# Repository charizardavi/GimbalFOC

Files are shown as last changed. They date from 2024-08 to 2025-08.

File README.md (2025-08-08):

# GimbalFOC

pcb image

## Sponsored By
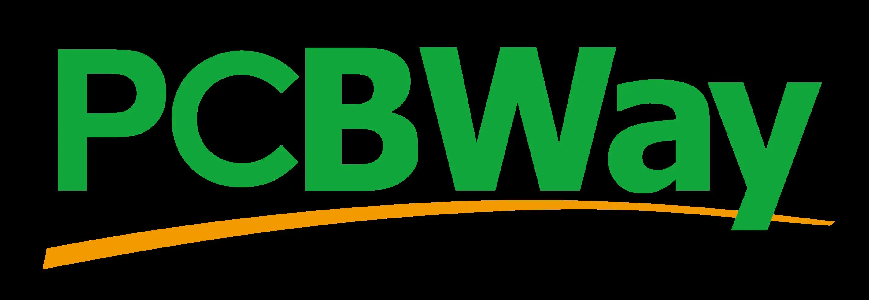
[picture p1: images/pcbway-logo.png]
pcbway logo


A gimbal BLDC controller:
- MCU: ESP32-S3 (XIAO)
- Motor Controller: DRV8813

## Other Parts
- [BLDC](https://shop.iflight.com/gimbal-motors-cat44/ipower-motor-gm4108h-120t-brushless-gimbal-motor-pro217)
- Battery: Tested with 4S LiPO

## Completed
- V1
- V2 (much smaller PCB, addition of ESP32S3)

## TODO
- Build and test 3-axis

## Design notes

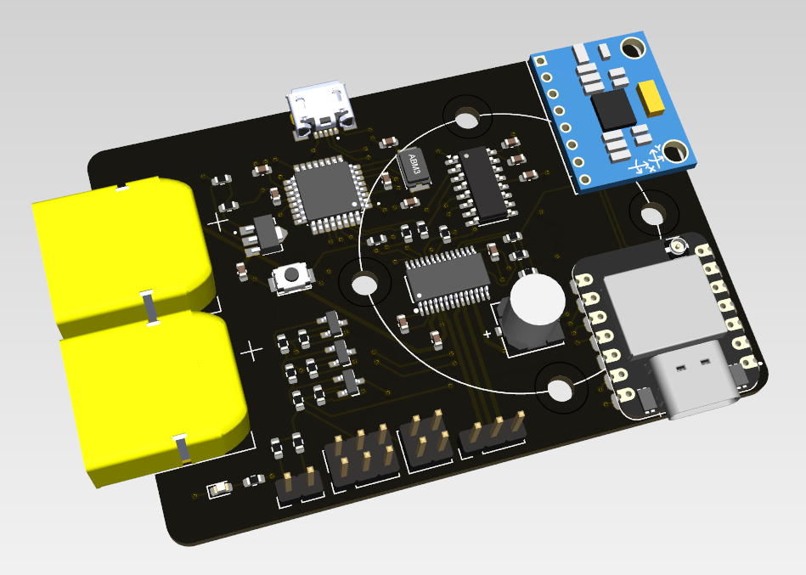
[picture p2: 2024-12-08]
images/kicad_preview.png

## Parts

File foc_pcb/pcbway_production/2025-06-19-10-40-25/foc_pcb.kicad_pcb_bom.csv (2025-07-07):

Designator | Quantity | Value | Footprint | Package | MPN | DNP | Mount_Type | Description | MF | Purchase-URL | Check_prices | STANDARD | PARTREV | SnapEDA_Link | MP | Description_1 | MANUFACTURER | DigiKey_Part_Number | SNAPEDA_PACKAGE_ID | MAXIMUM_PACKAGE_HEIGHT | Manufacturer Part | Manufacturer | Supplier Part | Supplier | LCSC Part Name
C1, C2, C4 | 3 | 100nF | C_0603_1608Metric |  |  |  | smt | Unpolarized capacitor
C3 | 1 | .1uF | C_0603_1608Metric |  |  |  | smt | Unpolarized capacitor
C5 | 1 | UWT1V101MCL1GS | PCAP_6.3x7.7-ELECT_NCA-L |  |  |  | smt | Polarized capacitor, US symbol
C6 | 1 | 470nF | C_0603_1608Metric |  |  |  | smt | Unpolarized capacitor
D1 | 1 | LED | LED_0603_1608Metric |  |  |  | smt | Light emitting diode
D2 | 1 | 1N5819HW-7-F | SOD3715X145N | None |  |  | smt |  | Diodes Zetex | https://www.snapeda.com/api/url_track_click_mouser/?unipart_id=4796063&manufacturer=Diodes Zetex&part_name=1N5819HW-7-F&search_term=None | https://www.snapeda.com/parts/1N5819HW-7-F/Zetex/view-part/?ref=eda | IPC-7351B | 18-2 | https://www.snapeda.com/parts/1N5819HW-7-F/Zetex/view-part/?ref=snap | 1N5819HW-7-F | Diode Schottky 40V 1A 2-Pin SOD-123 T/R | Diodes Inc.
J1 | 1 | Conn_01x03 | PinHeader_1x03_P2.54mm_Vertical |  |  |  | tht | Generic connector, single row, 01x03, script generated (kicad-library-utils/schlib/autogen/connector/)
J2 | 1 | BATT_IN | JST_VH_B2P-VH_1x02_P3.96mm_Vertical |  |  |  | tht | Generic connector, single row, 01x02, script generated (kicad-library-utils/schlib/autogen/connector/)
J3 | 1 | power_supply | PinHeader_2x02_P2.54mm_Vertical |  |  |  | tht | Generic connector, double row, 02x02, counter clockwise pin numbering scheme (similar to DIP package numbering), script generated (kicad-library-utils/schlib/autogen/connector/)
J4 | 1 | IMU | PinHeader_1x04_P2.00mm_Vertical |  |  |  | tht | Generic connector, single row, 01x04, script generated (kicad-library-utils/schlib/autogen/connector/)
J5 | 1 | ESP | PinHeader_1x04_P2.00mm_Vertical |  |  |  | tht | Generic connector, single row, 01x04, script generated (kicad-library-utils/schlib/autogen/connector/)
R1, R6, R8, R9 | 4 | 10k | R_0603_1608Metric |  |  |  | smt | Resistor
R10, R11 | 2 | 4.7k | R_0603_1608Metric |  |  |  | smt | Resistor
R2, R5, R7 | 3 | 1k | R_0603_1608Metric |  |  |  | smt | Resistor
R3 | 1 | 200 | R_0603_1608Metric |  |  |  | smt | Resistor
R4 | 1 | 590 | R_0603_1608Metric |  |  |  | smt | Resistor
U1 | 1 | DRV8313PWPR | HTSSOP-28_L9.8-W4.5-P0.65-LS6.6-BL-EP | HTSSOP-28 Texas Instruments |  |  | tht | 65-V max 3-A peak 3-phase motor driver with integrated FETs | Texas Instruments |  | https://www.snapeda.com/parts/DRV8313PWPR/Texas+Instruments/view-part/?ref=eda | Manufacturer Recommendations | D | https://www.snapeda.com/parts/DRV8313PWPR/Texas+Instruments/view-part/?ref=snap | DRV8313PWPR |  | Texas Instruments | 296-40072-2-ND | 102627 | 1.2 mm
U2 | 1 | ~ | SOP-8_L4.9-W3.9-P1.27-LS6.0-BL |  |  |  | tht |  |  |  |  |  |  |  |  |  |  |  |  |  | MT6701CT-STD | MagnTek(麦歌恩) | C2856764 | LCSC | 霍尔在线编程角度位置传感器
U3 | 1 | ~ | MOUDLE14P-SMD-2.54-21X17.8MM |  |  |  | tht
VR1 | 1 | LM317LCPK | VREG_LM317LCPK | SOT-89-3 Texas Instruments |  |  | smt |  | Texas Instruments | https://www.snapeda.com/api/url_track_click_mouser/?unipart_id=354472&manufacturer=Texas Instruments&part_name=LM317LCPK&search_term=None | https://www.snapeda.com/parts/LM317LCPK/Texas+Instruments/view-part/?ref=eda | Manufacturer Recommendations | E | https://www.snapeda.com/parts/LM317LCPK/Texas+Instruments/view-part/?ref=snap | LM317LCPK | 100-mA, 35-V, adjustable linear voltage regulator | Texas Instruments | 296-26093-2-ND | 102648 | 1.6 mm

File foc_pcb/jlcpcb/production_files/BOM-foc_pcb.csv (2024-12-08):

Comment | Designator | Footprint | LCSC
10k | R19 | R_0603_1608Metric
.1uF | C4 | C_0603_1608Metric
UWT1V101MCL1GS | C11 | PCAP_6.3x7.7-ELECT_NCA-L
1k | R7 | R_0603_1608Metric
BSS138-7-F | U3 | SOT95P240X110-3N
10k | R17 | R_0603_1608Metric
power_supply | J4 | PinHeader_2x02_P2.54mm_Vertical
1k | R6 | R_0603_1608Metric
SW_Push | SW1 | SW-SMD_L4.0-W3.0-LS4.6
200 | R13 | R_0603_1608Metric
10k | R2 | R_0603_1608Metric
BSS138-7-F | U4 | SOT95P240X110-3N
100nF | C9 | C_0603_1608Metric
10118193-0001LF | J12 | AMPHENOL_10118193-0001LF
XT60PW-M | J5 | AMASS_XT60PW-M
MPU6050 | J1 | PinHeader_1x08_P2.54mm_Vertical
100nF | C2 | C_0603_1608Metric
Conn_01x03 | J3 | PinHeader_1x03_P2.54mm_Vertical
DRV8313PWPR | U1 | HTSSOP-28_L9.8-W4.5-P0.65-LS6.6-BL-EP
10k | R15 | R_0603_1608Metric
1nF | C10 | C_0603_1608Metric
10k | R12 | R_0603_1608Metric
10k | R5 | R_0603_1608Metric
LED | D5 | LED_0603_1608Metric
100nF | C7 | C_0603_1608Metric
~ | U6 | MOUDLE14P-SMD-2.54-21X17.8MM
10k | R18 | R_0603_1608Metric
10nF | C12 | C_0603_1608Metric
22pF | C16 | C_0603_1608Metric
1k | R10 | R_0603_1608Metric
ABM3-16MHZ | Y1 | XTAL_ABM3-16.000MHZ-B2-T
100nF | C8 | C_0603_1608Metric
ATMEGA328P-AU | U2 | QFP80P900X900X120-32N
LM317LCPK | VR1 | VREG_LM317LCPK
10k | R1 | R_0603_1608Metric
Conn_01x02 | J2 | PinHeader_1x02_P2.54mm_Vertical
10k | R3 | R_0603_1608Metric
BSS138-7-F | U7 | SOT95P240X110-3N
22pF | C17 | C_0603_1608Metric
10k | R16 | R_0603_1608Metric
XT60PW-M | J6 | AMASS_XT60PW-M
CH340C | U5 | SOIC-16_3.9x9.9mm_P1.27mm
100nF | C3 | C_0603_1608Metric
10k | R20 | R_0603_1608Metric
10k | R8 | R_0603_1608Metric
10k | R4 | R_0603_1608Metric
100nF | C6 | C_0603_1608Metric
Conn_02x03_Top_Bottom | J10 | PinHeader_2x03_P2.54mm_Vertical
470nF | C1 | C_0603_1608Metric
590 | R14 | R_0603_1608Metric
1uF | C14 | C_0603_1608Metric
100nF | C13 | C_0603_1608Metric
AS5600-ASOT | IC1 | SOIC127P600X175-8N
4.7k | R9 | R_0603_1608Metric
4.7k | R11 | R_0603_1608Metric

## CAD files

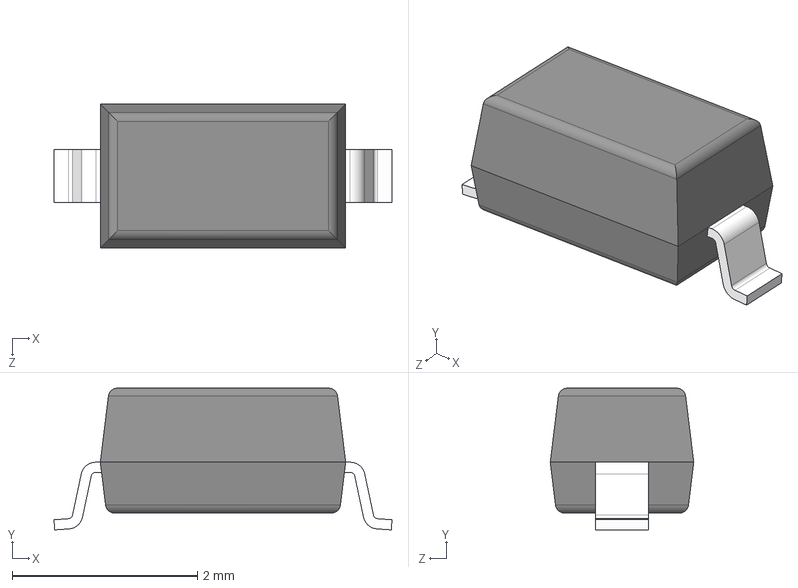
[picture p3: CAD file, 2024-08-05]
foc_pcb/parts_lib/1N5819HW-7-F/1N5819HW-7-F.step
3.65 x 1.53 x 1.55 mm

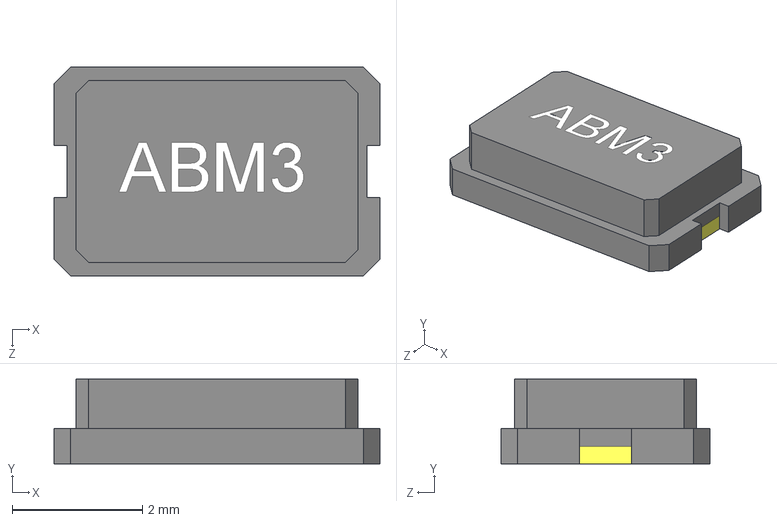
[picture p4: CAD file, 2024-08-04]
foc_pcb/parts_lib/ABM3-16.000MHZ-B2-T/ABM3-16.000MHZ-B2-T.step
5.00 x 1.30 x 3.20 mm

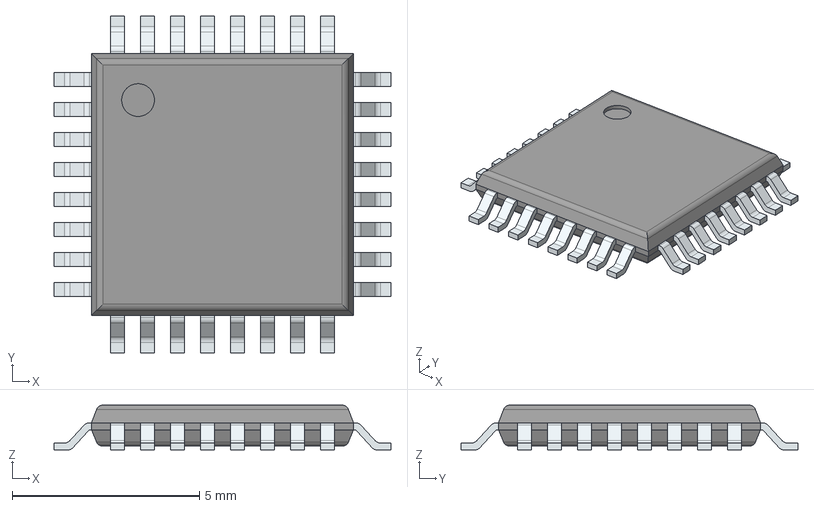
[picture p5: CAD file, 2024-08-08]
foc_pcb/parts_lib/ATMEGA328P-AU-NEW/ATMEGA328P-AU.stp
9.00 x 9.00 x 1.20 mm
PinsArrayLR
PinsArrayTB

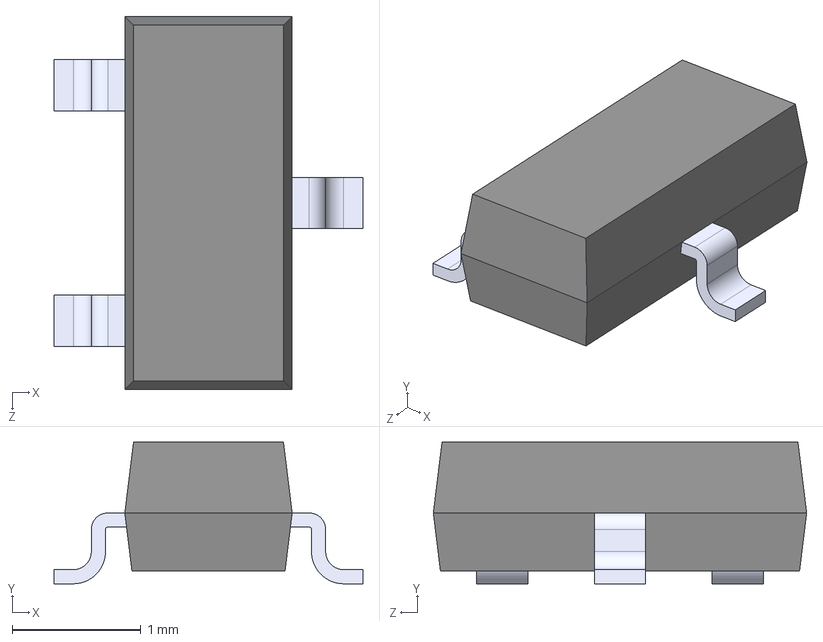
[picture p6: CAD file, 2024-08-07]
foc_pcb/parts_lib/BSS138-7-F/BSS138-7-F.step
2.40 x 1.10 x 2.90 mm

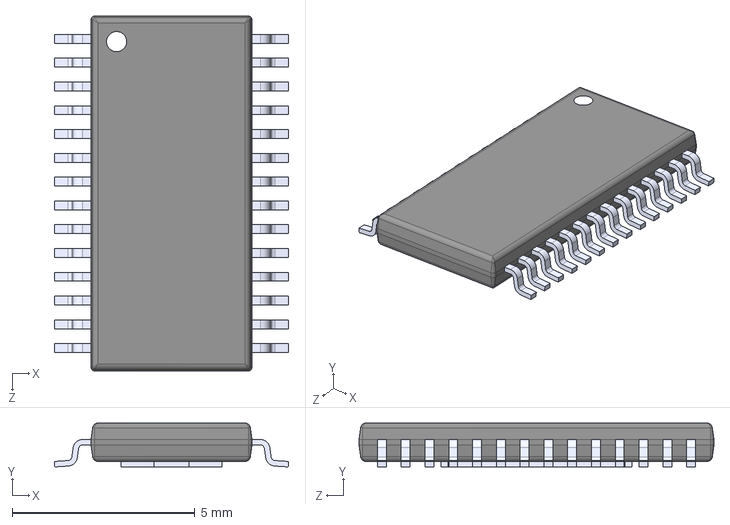
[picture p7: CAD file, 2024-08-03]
foc_pcb/parts_lib/DRV8313PWPR/DRV8313PWPR.step
6.40 x 1.20 x 9.70 mm

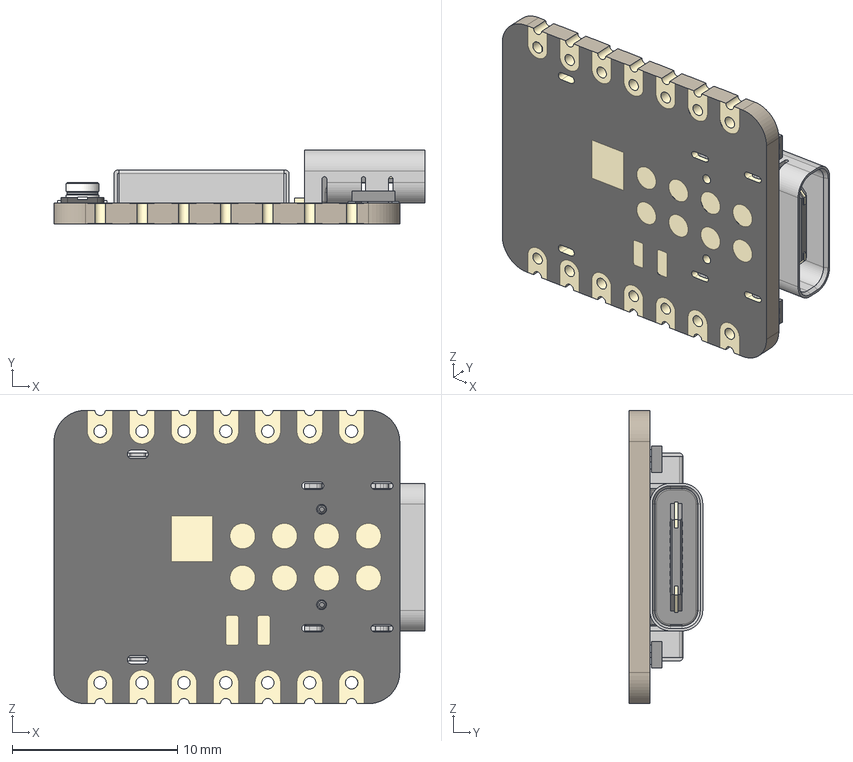
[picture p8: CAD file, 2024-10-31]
foc_pcb/parts_lib/ESP32S3/XIAO-ESP32S3 v2.step
22.5 x 4.46 x 17.8 mm
BOSS-EXTRUDE14_8_
BOSS-EXTRUDE7_4_
BOSS-EXTRUDE7_3_
BOSS-EXTRUDE14_4_
BOSS-EXTRUDE14_2_
BOSS-EXTRUDE14_11_
BOSS-EXTRUDE7_7_
BOSS-EXTRUDE14_9_
BOSS-EXTRUDE14_3_
BOSS-EXTRUDE14_7_
MIRROR2
BOSS-EXTRUDE14_5_
BOSS-EXTRUDE14_12_
BOSS-EXTRUDE7_8_
BOSS-EXTRUDE7_1_
BOSS-EXTRUDE14_10_
BOSS-EXTRUDE7_9_
BOSS-EXTRUDE14_6_
BOSS-EXTRUDE14_1_
BOSS-EXTRUDE7_6_
BOSS-EXTRUDE7_2_
CUT-EXTRUDE5
BOSS-EXTRUDE7_5_
Shield
Pins x 2
U.FL-R-SMT-1_10_ v1

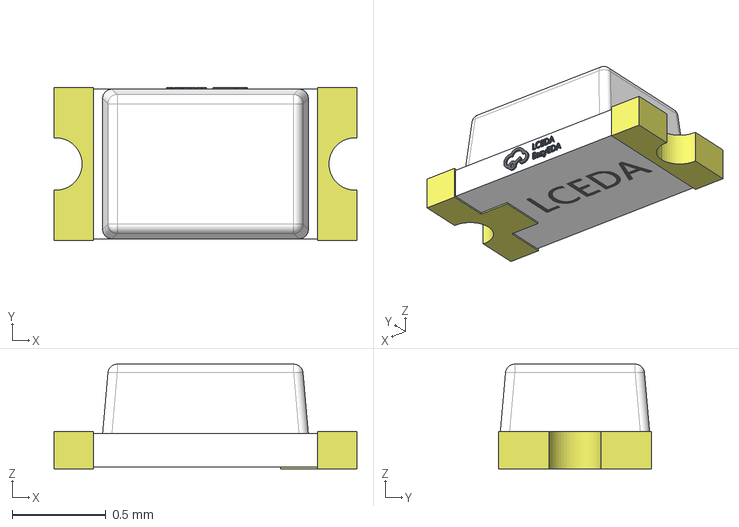
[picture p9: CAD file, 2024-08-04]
foc_pcb/parts_lib/KT-0603R/KT-0603R.step
1.62 x 0.82 x 0.56 mm

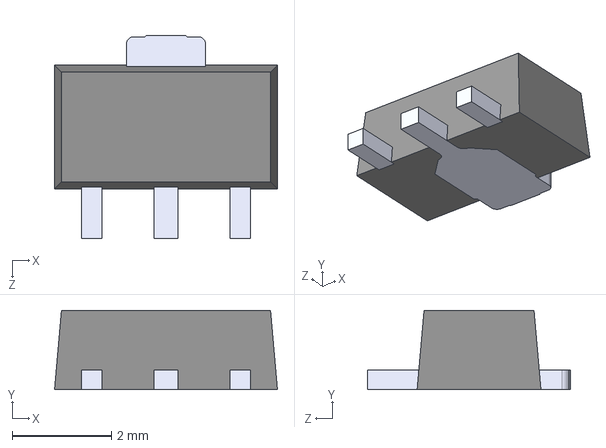
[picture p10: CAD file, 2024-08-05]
foc_pcb/parts_lib/LM317LCPK/LM317LCPK.step
4.50 x 1.60 x 4.09 mm

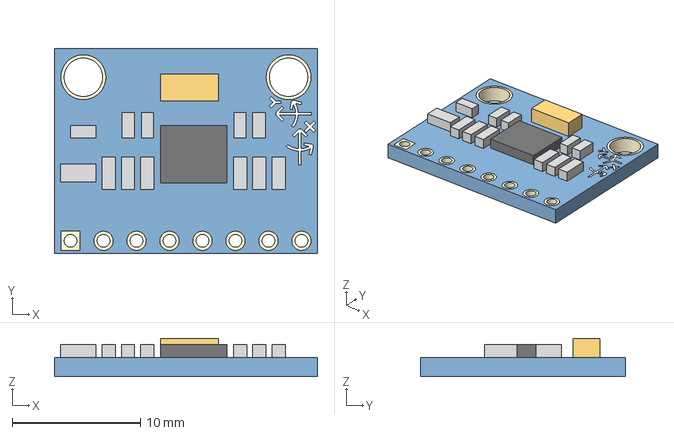
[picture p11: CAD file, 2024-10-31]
foc_pcb/parts_lib/MPU_6050/MPU_6050.step
20.5 x 16.0 x 3.00 mm

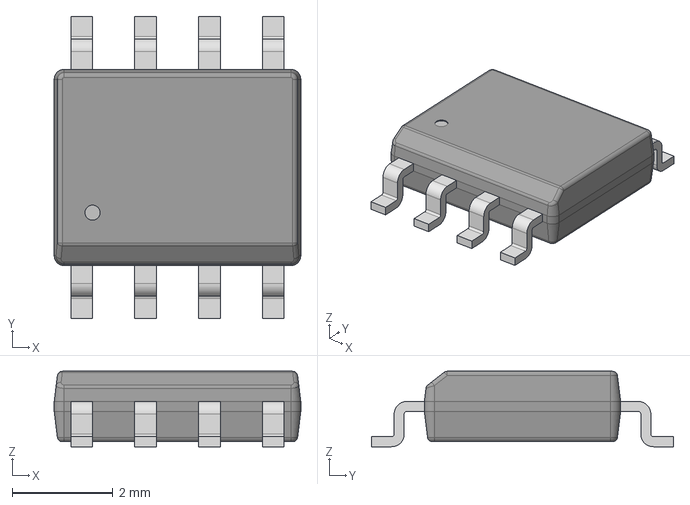
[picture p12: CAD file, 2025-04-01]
foc_pcb/parts_lib/MT6701CT-STD/MT6701CT-STD.step
4.90 x 6.00 x 1.50 mm

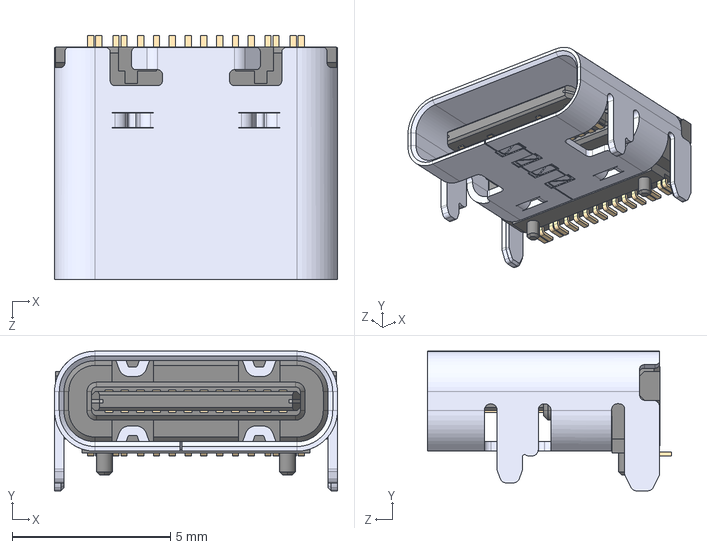
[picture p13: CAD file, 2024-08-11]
foc_pcb/parts_lib/USB4105-GF-A/USB4105-GF-A.step
8.94 x 4.41 x 7.71 mm

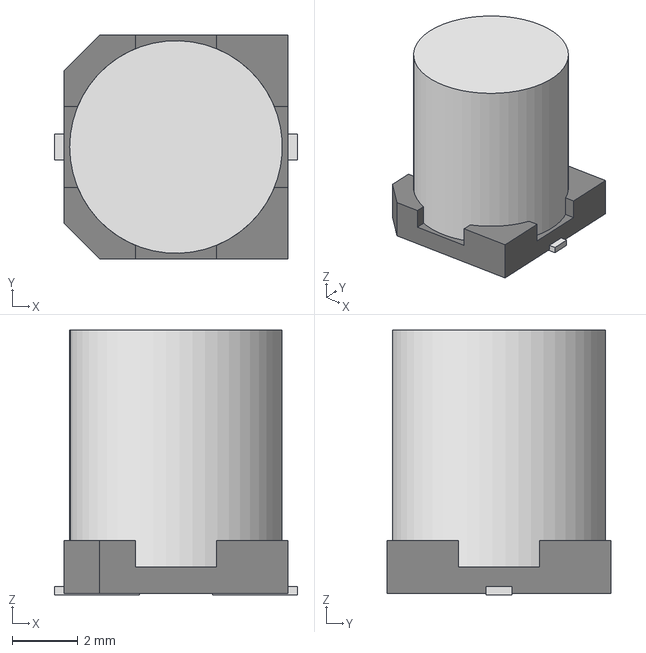
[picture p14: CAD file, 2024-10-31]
foc_pcb/parts_lib/UWT1V101MCL1GS/PCAP_6_3x7_7-ELECT_NCA.step
7.39 x 6.81 x 8.05 mm

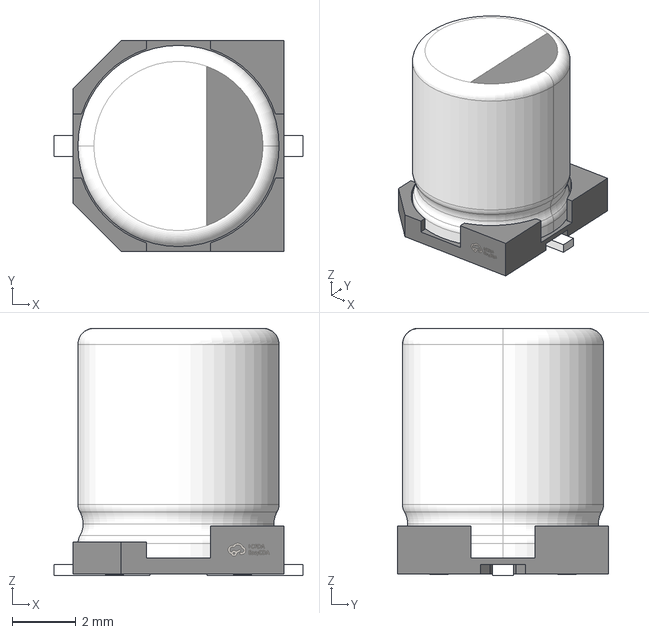
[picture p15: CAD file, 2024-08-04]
foc_pcb/parts_lib/VT1V101M-CRE77/VT1V101M-CRE77.step
7.80 x 6.60 x 7.75 mm

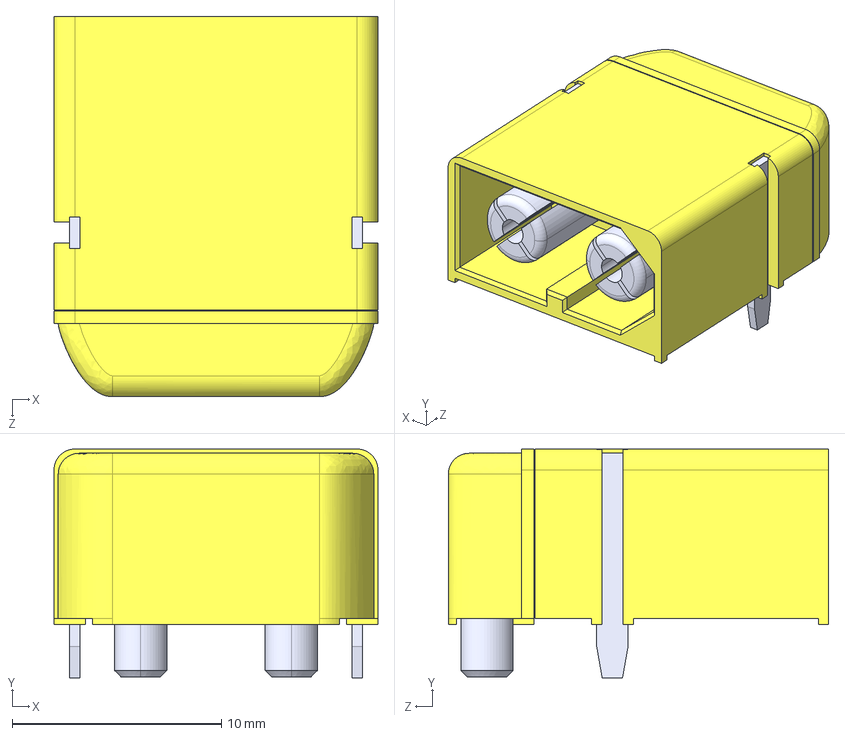
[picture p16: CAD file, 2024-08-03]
foc_pcb/parts_lib/XT60PW-M/XT60PW-M.step
15.5 x 11.0 x 18.2 mm

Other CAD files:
foc_pcb/parts_lib/ATMEGA328P-AU/ATMEGA328P-AU.step
foc_pcb/parts_lib/simpleFOC_led/simplefoc_LED.step
foc_pcb/parts_lib/YTS-A011-2B/YTS-A011-2B.step
foc_pcb/parts_lib/usbMicroB/10118193-0001LF.step

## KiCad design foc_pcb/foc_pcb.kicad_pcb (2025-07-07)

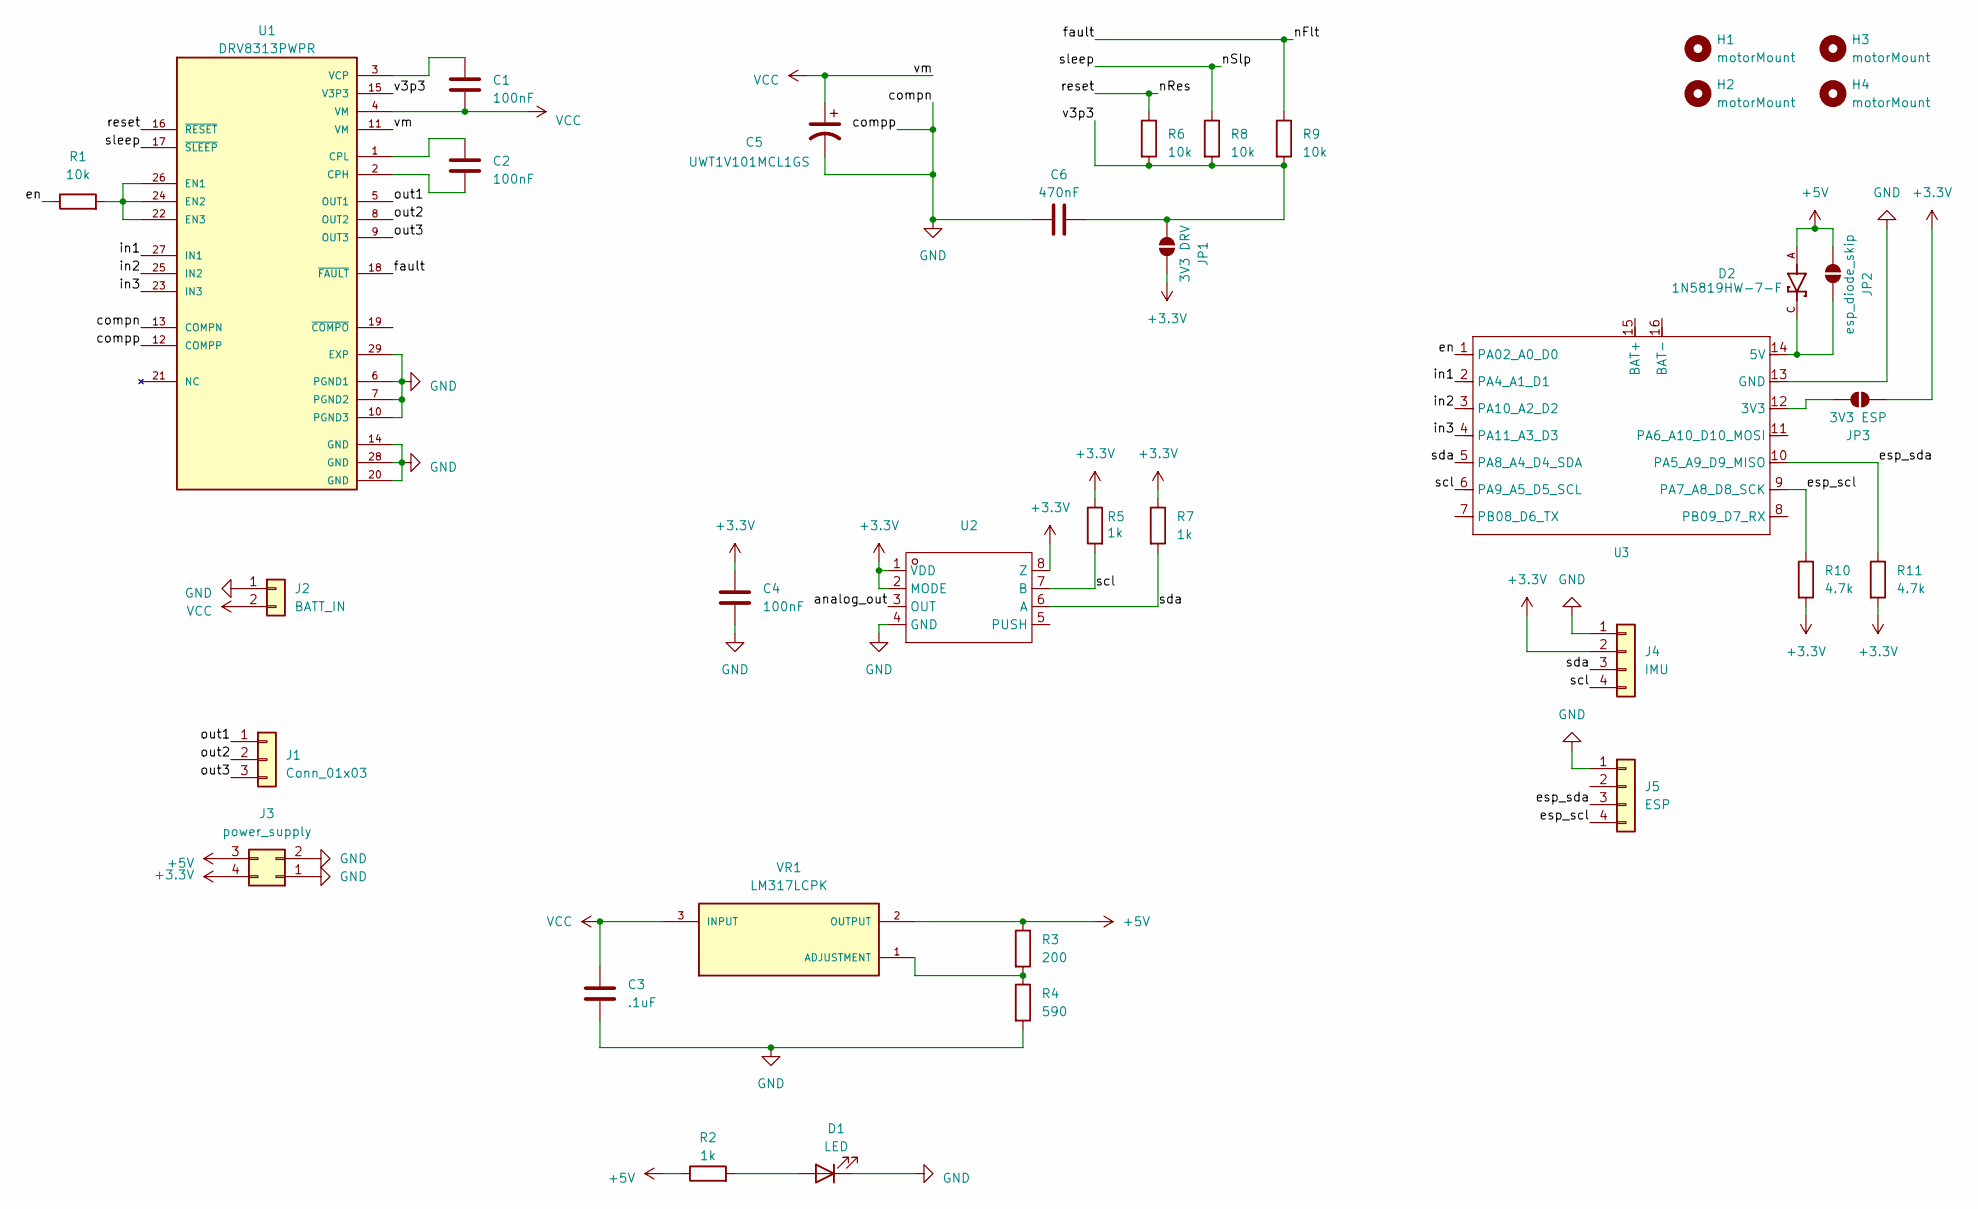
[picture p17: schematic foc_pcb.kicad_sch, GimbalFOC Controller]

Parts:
C1, C2, C4: 100nF; C_0603_1608Metric
C3: .1uF; C_0603_1608Metric
C5: UWT1V101MCL1GS; PCAP_6.3x7.7-ELECT_NCA-L
C6: 470nF; C_0603_1608Metric
D1: LED; LED_0603_1608Metric
D2: 1N5819HW-7-F; SOD3715X145N; PARTREV 18-2
H1, H2, H3, H4: motorMount; MountingHole_3.2mm_M3
J1: Conn_01x03; PinHeader_1x03_P2.54mm_Vertical
J2: BATT_IN; JST_VH_B2P-VH_1x02_P3.96mm_Vertical
J3: power_supply; PinHeader_2x02_P2.54mm_Vertical
J4: IMU; PinHeader_1x04_P2.00mm_Vertical
J5: ESP; PinHeader_1x04_P2.00mm_Vertical
JP1: 3V3 DRV; SolderJumper-2_P1.3mm_Open_TrianglePad1.0x1.5mm
JP2: esp_diode_skip; SolderJumper-2_P1.3mm_Open_TrianglePad1.0x1.5mm
JP3: 3V3 ESP; SolderJumper-2_P1.3mm_Open_TrianglePad1.0x1.5mm
R1, R6, R8, R9: 10k; R_0603_1608Metric
R2, R5, R7: 1k; R_0603_1608Metric
R3: 200; R_0603_1608Metric
R4: 590; R_0603_1608Metric
R10, R11: 4.7k; R_0603_1608Metric
U1: DRV8313PWPR; HTSSOP-28_L9.8-W4.5-P0.65-LS6.6-BL-EP; PARTREV D; DigiKey_Part_Number 296-40072-2-ND
U2: SOP-8_L4.9-W3.9-P1.27-LS6.0-BL; Manufacturer Part MT6701CT-STD; LCSC Part Name 霍尔在线编程角度位置传感器
U3: MOUDLE14P-SMD-2.54-21X17.8MM
VR1: LM317LCPK; VREG_LM317LCPK; PARTREV E; DigiKey_Part_Number 296-26093-2-ND

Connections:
+3.3V: C4.2, J3.4, J4.2, JP1.1 (A), JP3.2 (B), R5.1, R7.1, R10.2, R11.2, U2.1 (VDD), U2.2 (MODE), U2.8 (Z)
+5V: D2.A, J3.3, JP2.2 (B), R2.1, R3.1, VR1.2 (OUTPUT)
/analog_out: U2.3 (OUT)
/en: R1.1, U3.1 (PA02_A0_D0)
/esp_scl: J5.4, R10.1, U3.9 (PA7_A8_D8_SCK)
/esp_sda: J5.3, R11.1, U3.10 (PA5_A9_D9_MISO)
/fault: R9.1, U1.18 (~FAULT)
/in1: U1.27 (IN1), U3.2 (PA4_A1_D1)
/in2: U1.25 (IN2), U3.3 (PA10_A2_D2)
/in3: U1.23 (IN3), U3.4 (PA11_A3_D3)
/nRes: R6.1, U1.16 (~RESET)
/nSlp: R8.1, U1.17 (~SLEEP)
/out1: J1.1, U1.5 (OUT1)
/out2: J1.2, U1.8 (OUT2)
/out3: J1.3, U1.9 (OUT3)
/scl: J4.4, R5.2, U2.7 (B), U3.6 (PA9_A5_D5_SCL)
/sda: J4.3, R7.2, U2.6 (A), U3.5 (PA8_A4_D4_SDA)
/v3p3: C6.2, JP1.2 (B), R6.2, R8.2, R9.2, U1.15 (V3P3)
GND: C3.2, C4.1, C5.2, C6.1, D1.1 (K), J2.1, J3.1, J3.2, J4.1, J5.1, R4.2, U1.6 (PGND1), U1.7 (PGND2), U1.10 (PGND3), U1.12 (COMPP), U1.13 (COMPN), U1.14 (GND), U1.20 (GND), U1.28 (GND), U1.29 (EXP), U2.4 (GND), U3.13 (GND)
unnamed: D1.2 (A), R2.2
unnamed: D2.C, JP2.1 (A), U3.14 (5V)
unnamed: JP3.1 (A), U3.12 (3V3)
unnamed: C2.2, U1.2 (CPH)
unnamed: C2.1, U1.1 (CPL)
unnamed: R1.2, U1.22 (EN3), U1.24 (EN2), U1.26 (EN1)
unnamed: C1.1, U1.3 (VCP)
unnamed: R3.2, R4.1, VR1.1 (ADJUSTMENT)
VCC: C1.2, C3.1, C5.1, J2.2, U1.4 (VM), U1.11 (VM), VR1.3 (INPUT)

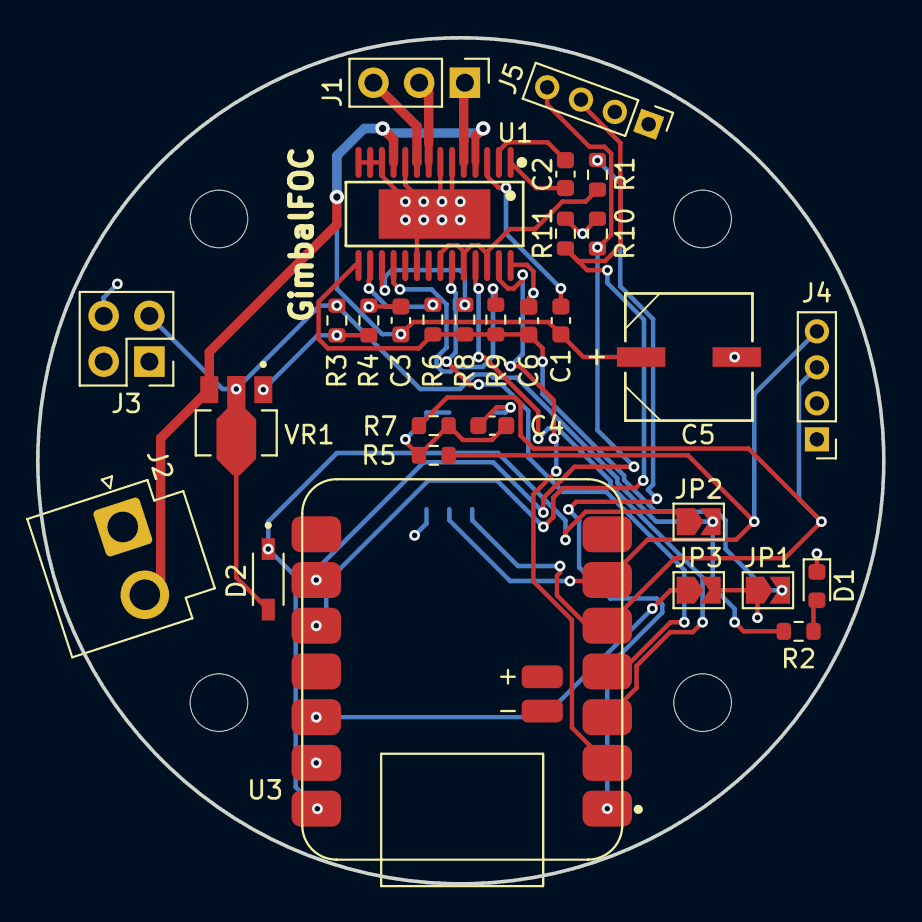
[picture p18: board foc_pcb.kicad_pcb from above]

Board: 4 copper layers, 47.0 x 47.0 mm, 35 parts (1 on the bottom side), 27 nets.

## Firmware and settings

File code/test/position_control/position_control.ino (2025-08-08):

#include "MT6701.hpp"
#include <SimpleFOC.h>

MT6701  encoder;
float   readMt6701() { return encoder.getAngleRadians(); }
void    initMt6701() { encoder.begin(); }
GenericSensor sensor(readMt6701, initMt6701);

BLDCMotor       motor  = BLDCMotor(11, 5.55f, 100);
BLDCDriver3PWM  driver = BLDCDriver3PWM(D1, D2, D3, D0);

Commander commander = Commander(Serial);

void onMotor(char* cmd){ commander.motor(&motor, cmd); }

void zeroPids(char*) {
  motor.PID_velocity.reset();
  motor.P_angle.reset();
  Serial.println(F("PIDs reset"));
}

void setup() {
  Serial.begin(115200);
  while(!Serial);

  driver.voltage_power_supply = 15;
  driver.pwm_frequency = 25000;
  driver.init();
  motor.linkDriver(&driver);

  sensor.init();
  motor.linkSensor(&sensor);

  motor.controller = MotionControlType::angle;
  motor.current_limit = 0.7;
  motor.voltage_limit = 6;
  // motor.velocity_limit = 4;

  motor.PID_velocity.P = 0.2;
  motor.PID_velocity.I = 20;
  motor.LPF_velocity.Tf = 0.01; 

  motor.P_angle.P = 5;

  motor.useMonitoring(Serial);

  motor.zero_electric_angle = 2.251883;
  motor.sensor_direction = Direction::CCW;

  motor.init();
  motor.initFOC();
  Serial.println("FOC ready (position control)");


  commander.add('M', onMotor);
  commander.add('Z', zeroPids, "zero pids");
}

void loop() {
  motor.loopFOC();
  motor.move(2.0f);

  commander.run();
}

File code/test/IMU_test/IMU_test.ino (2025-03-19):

#define QUAT_ANIMATION // Uncomment this line to output data in the correct format for ZaneL's Node.js Quaternion animation tool: https://github.com/ZaneL/quaternion_sensor_3d_nodejs

#include "ICM_20948.h"  // Click here to get the library: http://librarymanager/All#SparkFun_ICM_20948_IMU

//#define USE_SPI       // Uncomment this to use SPI

#define SERIAL_PORT Serial

#define SPI_PORT SPI  // Your desired SPI port.       Used only when "USE_SPI" is defined
#define CS_PIN 2      // Which pin you connect CS to. Used only when "USE_SPI" is defined

#define WIRE_PORT Wire  // Your desired Wire port.      Used when "USE_SPI" is not defined
// The value of the last bit of the I2C address.
// On the SparkFun 9DoF IMU breakout the default is 1, and when the ADR jumper is closed the value becomes 0
#define AD0_VAL 1

#ifdef USE_SPI
ICM_20948_SPI myICM;  // If using SPI create an ICM_20948_SPI object
#else
ICM_20948_I2C myICM;  // Otherwise create an ICM_20948_I2C object
#endif

void setup() {

  SERIAL_PORT.begin(115200);  // Start the serial console
#ifndef QUAT_ANIMATION
  SERIAL_PORT.println(F("ICM-20948 Example"));
#endif

  delay(100);

#ifndef QUAT_ANIMATION
  while (SERIAL_PORT.available())  // Make sure the serial RX buffer is empty
    SERIAL_PORT.read();

  SERIAL_PORT.println(F("Press any key to continue..."));

  while (!SERIAL_PORT.available())  // Wait for the user to press a key (send any serial character)
    ;
#endif

#ifdef USE_SPI
  SPI_PORT.begin();
#else
  WIRE_PORT.begin(5, 6);
  WIRE_PORT.setClock(400000);
#endif

#ifndef QUAT_ANIMATION
  //myICM.enableDebugging(); // Uncomment this line to enable helpful debug messages on Serial
#endif

  bool initialized = false;
  while (!initialized) {

    // Initialize the ICM-20948
    // If the DMP is enabled, .begin performs a minimal startup. We need to configure the sample mode etc. manually.
#ifdef USE_SPI
    myICM.begin(CS_PIN, SPI_PORT);
#else
    myICM.begin(WIRE_PORT, AD0_VAL);
#endif

#ifndef QUAT_ANIMATION
    SERIAL_PORT.print(F("Initialization of the sensor returned: "));
    SERIAL_PORT.println(myICM.statusString());
#endif
    if (myICM.status != ICM_20948_Stat_Ok) {
#ifndef QUAT_ANIMATION
      SERIAL_PORT.println(F("Trying again..."));
#endif
      delay(500);
    } else {
      initialized = true;
    }
  }

#ifndef QUAT_ANIMATION
  SERIAL_PORT.println(F("Device connected!"));
#endif

  bool success = true;  // Use success to show if the DMP configuration was successful

  // Initialize the DMP. initializeDMP is a weak function. You can overwrite it if you want to e.g. to change the sample rate
  success &= (myICM.initializeDMP() == ICM_20948_Stat_Ok);

  // DMP sensor options are defined in ICM_20948_DMP.h
  //    INV_ICM20948_SENSOR_ACCELEROMETER               (16-bit accel)
  //    INV_ICM20948_SENSOR_GYROSCOPE                   (16-bit gyro + 32-bit calibrated gyro)
  //    INV_ICM20948_SENSOR_RAW_ACCELEROMETER           (16-bit accel)
  //    INV_ICM20948_SENSOR_RAW_GYROSCOPE               (16-bit gyro + 32-bit calibrated gyro)
  //    INV_ICM20948_SENSOR_MAGNETIC_FIELD_UNCALIBRATED (16-bit compass)
  //    INV_ICM20948_SENSOR_GYROSCOPE_UNCALIBRATED      (16-bit gyro)
  //    INV_ICM20948_SENSOR_STEP_DETECTOR               (Pedometer Step Detector)
  //    INV_ICM20948_SENSOR_STEP_COUNTER                (Pedometer Step Detector)
  //    INV_ICM20948_SENSOR_GAME_ROTATION_VECTOR        (32-bit 6-axis quaternion)
  //    INV_ICM20948_SENSOR_ROTATION_VECTOR             (32-bit 9-axis quaternion + heading accuracy)
  //    INV_ICM20948_SENSOR_GEOMAGNETIC_ROTATION_VECTOR (32-bit Geomag RV + heading accuracy)
  //    INV_ICM20948_SENSOR_GEOMAGNETIC_FIELD           (32-bit calibrated compass)
  //    INV_ICM20948_SENSOR_GRAVITY                     (32-bit 6-axis quaternion)
  //    INV_ICM20948_SENSOR_LINEAR_ACCELERATION         (16-bit accel + 32-bit 6-axis quaternion)
  //    INV_ICM20948_SENSOR_ORIENTATION                 (32-bit 9-axis quaternion + heading accuracy)

  // Enable the DMP orientation sensor
  success &= (myICM.enableDMPSensor(INV_ICM20948_SENSOR_ORIENTATION) == ICM_20948_Stat_Ok);

  // Enable any additional sensors / features
  //success &= (myICM.enableDMPSensor(INV_ICM20948_SENSOR_RAW_GYROSCOPE) == ICM_20948_Stat_Ok);
  //success &= (myICM.enableDMPSensor(INV_ICM20948_SENSOR_RAW_ACCELEROMETER) == ICM_20948_Stat_Ok);
  //success &= (myICM.enableDMPSensor(INV_ICM20948_SENSOR_MAGNETIC_FIELD_UNCALIBRATED) == ICM_20948_Stat_Ok);

  // Configuring DMP to output data at multiple ODRs:
  // DMP is capable of outputting multiple sensor data at different rates to FIFO.
  // Setting value can be calculated as follows:
  // Value = (DMP running rate / ODR ) - 1
  // E.g. For a 5Hz ODR rate when DMP is running at 55Hz, value = (55/5) - 1 = 10.
  success &= (myICM.setDMPODRrate(DMP_ODR_Reg_Quat9, 0) == ICM_20948_Stat_Ok);  // Set to the maximum
  //success &= (myICM.setDMPODRrate(DMP_ODR_Reg_Accel, 0) == ICM_20948_Stat_Ok); // Set to the maximum
  //success &= (myICM.setDMPODRrate(DMP_ODR_Reg_Gyro, 0) == ICM_20948_Stat_Ok); // Set to the maximum
  //success &= (myICM.setDMPODRrate(DMP_ODR_Reg_Gyro_Calibr, 0) == ICM_20948_Stat_Ok); // Set to the maximum
  //success &= (myICM.setDMPODRrate(DMP_ODR_Reg_Cpass, 0) == ICM_20948_Stat_Ok); // Set to the maximum
  //success &= (myICM.setDMPODRrate(DMP_ODR_Reg_Cpass_Calibr, 0) == ICM_20948_Stat_Ok); // Set to the maximum

  // Enable the FIFO
  success &= (myICM.enableFIFO() == ICM_20948_Stat_Ok);

  // Enable the DMP
  success &= (myICM.enableDMP() == ICM_20948_Stat_Ok);

  // Reset DMP
  success &= (myICM.resetDMP() == ICM_20948_Stat_Ok);

  // Reset FIFO
  success &= (myICM.resetFIFO() == ICM_20948_Stat_Ok);

  // Check success
  if (success) {
#ifndef QUAT_ANIMATION
    SERIAL_PORT.println(F("DMP enabled!"));
#endif
  } else {
    SERIAL_PORT.println(F("Enable DMP failed!"));
    SERIAL_PORT.println(F("Please check that you have uncommented line 29 (#define ICM_20948_USE_DMP) in ICM_20948_C.h..."));
    while (1)
      ;  // Do nothing more
  }
}
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

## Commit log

2024-08-03 schema v1 done
    [AS5600-ASOT.step, ATMEGA328P-AU.step, CH340G.step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]
2024-08-03 added power connectors, temp commit for 8.0 migration
    [X322516MLB4SI.step, XT60PW-M.step, foc_pcb.kicad_pcb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]
2024-08-04 migrated, saving old lm2596
    [ABM3-16.000MHZ-B2-T.step, CH340G.step, KT-0603R.step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]
2024-08-04 added todo
    [SK32WA.step, SK33-TP.step, foc_pcb.kicad_pcb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]
2024-08-05 fixed regulator, schema done (?)
    [1N5819HW-7-F.step, LM317LCPK.step, SK33-TP.step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]
2024-08-05 added motor mount
    [SPM6530T-R47M170.step, foc_pcb.kicad_pcb, foc_pcb.kicad_sch]
2024-08-07 added level shifter, layout done
    [BSS138-7-F.step, foc_pcb.kicad_pcb, foc_pcb.kicad_sch]
2024-08-08 backup in case footprint swap fails
    [foc_pcb.kicad_pcb]
2024-08-08 swapped footprint, fixed several DRC violations
    [ATMEGA328P-AU.stp, foc_pcb.kicad_pcb, foc_pcb.kicad_sch]
2024-08-10 added thicker tracks for vcc
    [foc_pcb.kicad_pcb]
2024-08-11 before switch usb
    [USB4105-GF-A.step, foc_pcb.kicad_pcb, foc_pcb.kicad_sch]
2024-08-11 reverted to old usb, pray to jlc gods
    [foc_pcb.kicad_pcb, foc_pcb.kicad_sch]
2024-08-12 board v1 done, to be ordered soon
    [10118193-0001LF.step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]
2024-08-22 readme updated
    [foc_pcb.kicad_pcb, foc_pcb.kicad_sch]
2024-08-26 added test scripts, as5600 working, drv tbd
    [foc_pcb.kicad_pcb]
2024-10-30 foc code done, pre-redesign
    [sensor_parameter_finder.ino, velocity_control.ino]
2024-10-31 V2 redesign done, needs review
    [10118193-0001LF.step, 1N5819HW-7-F.step, ABM3-16.000MHZ-B2-T.step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]
2024-10-31 fixes parts lib folder hopefully
    [10118193-0001LF.step, 1N5819HW-7-F.step, ABM3-16.000MHZ-B2-T.step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]
2024-11-01 compacted layout, finished V2
    [foc_pcb.kicad_pcb, foc_pcb.kicad_sch]
2024-11-13 fixed some drc and added silkscreen
    [foc_pcb.kicad_pcb]
2024-11-29 v1 assembled and firmware completed, some PID tuning required
2024-12-08 added kicad preview
    [BOM-foc_pcb.csv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]
2024-12-08 fixed kicad preview
2025-03-19 V2 FOC and SPI working
    [foc_pcb-F_Paste.dxf, foc_pcb.kicad_pcb]
2025-03-21 V3 Intial Commit
    [foc_pcb.kicad_pcb, foc_pcb.kicad_sch]
2025-03-22 readme update
    [foc_pcb.kicad_pcb]
2025-03-26 temp commit before re-layout
    [foc_pcb.kicad_pcb]
2025-04-01 removed rendunant solder jumpers
    [AS5600-ASOT.step, MT6701CT-STD.step, foc_pcb.kicad_pcb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]
2025-07-07 v3 incoming
    [foc_pcb-B_Cu.gbr, foc_pcb-B_Mask.gbr, foc_pcb-B_Paste.gbr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]
2025-07-13 open loop works
    [foc_pcb-F_Paste.dxf, foc_pcb.kicad_pcb, foc_pcb.kicad_sch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]
2025-08-08 fix readme, add tests
    [foc_pcb.kicad_pcb]
